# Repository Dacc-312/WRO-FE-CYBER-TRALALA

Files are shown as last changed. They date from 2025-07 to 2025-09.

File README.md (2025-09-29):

Cyber Tralala - WRO Future Engineers 2025
====

We are Cesar Escarrá, Diego Concepción and Christopher Vásquez. We are students from Thomas Jefferson School Of Panama and we are the members of the team Cyber Tralala that competes in the WRO 2025 Future Engineers Category. In this Repository, we share all the information of our project.  

Somos Cesar Escarrá, Diego Concepción y Christopher Vásquez. Somos estudiantes del Thomas Jefferson School y conformamos el equipo Cyber Tralala que participa en la categoria de futuros ingenieros de la WRO. En este repositorio compartimos toda la informacion de nuestro proyecto.  

## Project summary / Resumen del proyecto
  
Tralalerito is our self-driving car built for the WRO 2025 Future Engineers category. Our goal is to design a small, reliable robot that can navigate the Open Course and the Obstacle Course without any human control.  

Tralalerito es nuestro carro autónomo para la categoría Futuros Ingenieros de WRO 2025. Nuestro objetivo es diseñar un robot pequeño y confiable que pueda completar el Desafio Abierto y el Desafio de Obstaculos sin control humano.  

  

The robot uses a mix of simple sensors and a camera to “see” walls and colored signs on the field. It decides which way to turn and how to move using a program we created.  

We focused on making our car robust, simple and easy to maintain so it can handle the challenges during competition.  

El robot usa una combinación de sensores simples y una cámara para “ver” las paredes y las señales de colores en el campo. Con esa información, toma decisiones sobre cómo girar y avanzar usando un programa creado por nosotros.  

Nos enfocamos en que nuestro carro fuera resistente, simple y fácil de mantener para poder afrontar los retos durante la competencia.  

## Table of Content/ Tabla de Contenido 

* `t-photos` contains  photos of the team - Contiene las fotos de nuestro equipo.
* `v-photos` contains photos of the vehicle - Contiene las fotos de nuestro vehículo.
* `video` contains the video.md file with the link to a video where driving demonstration exists - Contiene los archivos con links a videos de youtube con el funcionamiento del robot.
* `schemes` contains one schematic diagrams in form of PNG and Fritzing of the electromechanical components illustrating all the elements (electronic components and motors) used in the vehicle and how they connect to each other - Contiene un diagrama electromecanico en formato PNG y Fritzing ilustrando todos los componentes usados en el vehiculo y sus debidas conexiones.
* `src` contains code of control software for all components which were programmed to participate in the competition - Contiene la programación usada en nuestro vehiculo para participar en la competencia.
* `models` is for the files for models used by 3D printers produce the vehicle elements - Contiene los modelos 3D utilizados para imprimir piezas para nuestro vehiculo.
* `other` is for other files which can be used to understand how to prepare the vehicle for the competition. It includes datasets, hardware specifications, communication protocols descriptions, links for buying, etc - Contiene especificaciones de hardware, protocolos de comunicacion, links de compra y otros.

 ## Team Members / Miembros del Equipo  

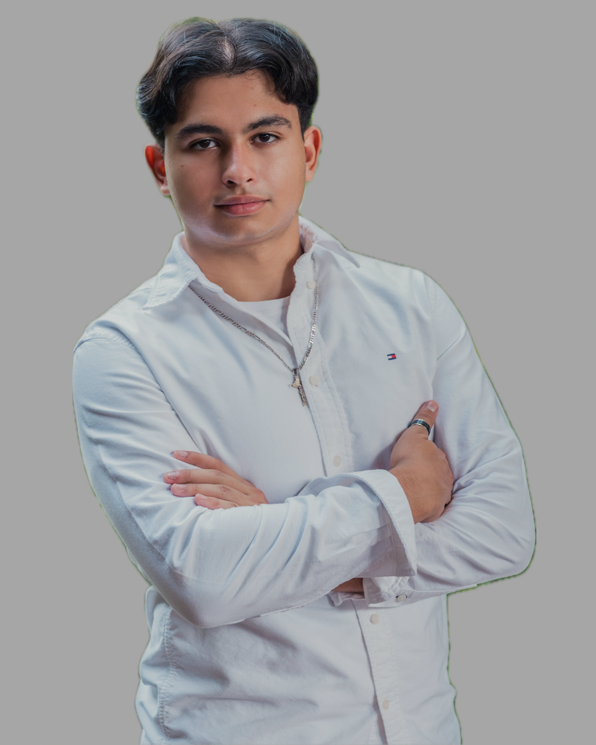
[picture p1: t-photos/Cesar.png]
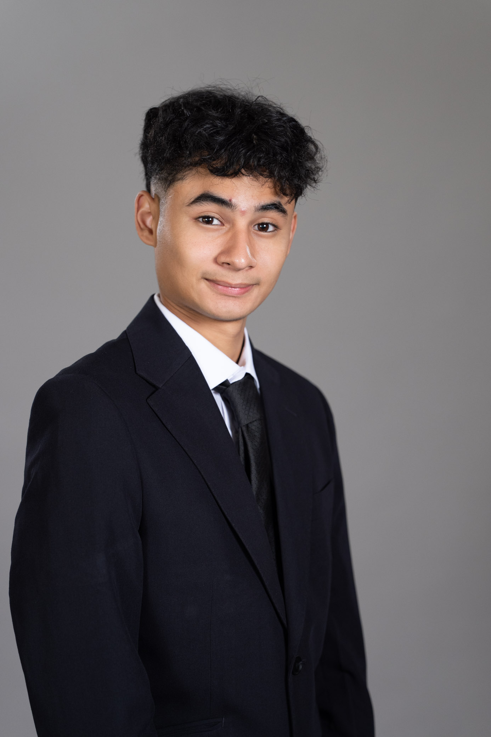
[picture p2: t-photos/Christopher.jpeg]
|  |   |   |
|:---:|:---:|:---:|
| **Diego Concepción**<br>17 years old | **Cesar Escarrá**<br>18 years old | **Christopher Vasquéz**<br>18 years old |

## Robot construction info / Información sobre la construcción y funcionamiento del robot

**Mobility management / Manejo de movilidad**

We decided to use a rear-wheel drive remote control car as the basis for our project. A remote control car provides a fairly resistant chassis in addition to bringing 6v motors for movement and direction, allowing us high speed if necessary. The steering of our car consists of a direct current motor which operates a rack and pinion system to give direction to the front axle.The traction system consist on a simple axle with a gear that is attached to the pinion of the motor. Many cuts were made to the original chassis to be able to remove the original circuits and place our circuits. We also desgined and printed 3D mounts for our sensors and camera. On top of that, we designed and printed a Cybertruck body to give protection to the internal parts and electronics.
  
Decidimos usar como base para proyecto un carro a control remoto de tracción trasera. Un carro a control remoto nos da un chasis resistente, adicional de tener el sistema de tracción y dirección con los motores de 6v necesarios para ello, y nos permite usar el auto a altas velocidades si es necesario. La direccion de nuestro vehículo consiste en un motor de corriente continua que opera un sistema de cremallera y piñon que dan el giro a los ejes delanteros. El sistema de tracción consiste en un eje solido conectado a las 2 ruedas traseras y a un engranaje que recibe el movimiento de el piñon del motor trasero. Le hicimos diversas modificaciones al chasis para poder quitar los controladores y circuitos originales y hacer espacio para colocar los nuestros. Le añadimos soportes impresos en 3D al chasis para poder colocar nuestros sensores y nuestra camara. Adicionalmente, diseñamos e imprimimos en 3D una carroceria de Cybertruck para cubrir y proteger los componentes electronicos y demas componentes internos del vehiculo.

**Power management / Manejo de potencia eléctrica**

For this project we decided to eliminate the car's original power source which was AA batteries and use 2 18650 lithium ion batteries connected in series because they have a much greater discharge capacity than AA batteries, in addition to having more capacity and more voltage (3.7V each one, making a total of 7.4V in series). These batteries are widely used from flashlights to electric vehicles, this way we ensure that it is easy to get chargers and spare parts.

Para este proyecto decidimos eliminar la fuente de poder original del auto que eran 2 baterias AA, y usamos 2 baterias 18650 de iones de litio conectados en serie, porque tiene una capacidad de descarga mucho mayor, aparte de tener una mayor capacidad y un mayor voltaje (3.7V cada una, totalizando 7.4V en serie). Estas baterias son ampliamente usadas, desde en linternas como en vehiculos electricos, así nos aseguramos que podemos conseguir fácilmente cargadores y repuestos.

**Obstacle and sense management / Manejo de visión y obstaculos**

For this project we decided to use hc-sr04 ultrasonic sensors because they are cheap, easy to obtain and have fairly low consumption. We are using two sensors, one on each side, to detect the distance to the walls on the sides so that we can make corner turns and stay without crashing in the open challenge. In the case of the obstacle challenge, the sensors still play a secondary role in helping to turn and prevent the car from crashing into walls.

For obstacle management we decided to use a Huskylens camera. This camera is very intuitive to use and has artificial intelligence which helps with detection, in this case of colors. The camera provides very good integration with the Microbit platform in addition to the ability to program new colors in just seconds.

Para ese proyecto decidimos utilizar sensores ultrasónicos HC-SR04 porque son baratos, fácil de obtener y tienen un consumo muy bajo. Estamos utilizando dos sensores, uno en el lado izquierdo y el otro en el derecho para obtener la distancia hasta las paredes laterales y poder tomar las curvas sin chocar en el desafio abierto. En el caso del desafio de obstaculos, los sensores igual toman un rol secundario en ayudar a girar y prevenir que el vehiculo choque.  

Para detectar los obstaculos, decidimos utilizar una camara Huskylens. Seleccionamos esta camara porque es muy intuitiva y tiene integrada una inteligencia artificial que ayuda con la deteteccion, en este caso de los colores. La camara tiene una muy buena integracion con la prataforma de microbit y tiene la capacidad de aprender colores en segundos.  
  
**Open Challenge Programming / Programación Desafío Abierto**

To program the open circuit, we use simple programming based on the two ultrasonic sensors. First, the ultrasonic variable and the elapsed time in the loop are established to have a constant reading, a conditional is placed to activate the H-bridge so that the rear motor goes forward with a constant speed until the elapsed time is the equivalent to 3 turns, where it stops moving. Now we place a condition, If our sensor detects a distance greater than 1.5 meters to one side, this means that the car must be turned to that side by activating the H-bridge corresponding to that direction of the front motor. Afterwards, if the sensors detect a distance greater than 30 cm on each side (which means that it is in the center) the car will advance straight, otherwise, the car will look for which of the two sides the measurement is less than 30cm to turn in the other direction and rectify.  

Para el circuito sin obstaculos, utilizamos una programacion simple basada en los dos sensores ultrasonicos. Primero, las variables de las distancias y el tiempo transcurrido se establecen en el bucle para tener una medicion constante. Colocamos una condicional para activar el Puente-H para que el motor avance con una velocidad constante hasta que el tiempo transcurrido corresponda al de las 3 vueltas, donde se detiene. Ahora colocamos una condicional, si nuestros sensores miden una distancia mayor a 1.5 metros en un lado, el vehiculo se mueve en esa direccion activando el puente H y por consecuencia el motor para que la direccion gire al lado adecuado. Despues, si los sensores miden una distancia mayor a 30cm en ambos lados (Esto significa que el robot esta en el centro) el carro avanzara recto, sino, el carro va a determinar de que lado la distancia es menor a 30cm para girar en la otra direccion y rectificar.

**Programming challenge obstacles / Programación desafío de obstaculos**

To begin, we first activate the huskylens in I2C protocol to communicate with the microbit and place it in color detection mode. After that, we have a secuence to drive out the parking lot, where it uses the ultrasonic sensors to determine where is the closest wall and then proceeds to go forward and backwards until its completely out of the parking space. In addition, we start with the rear motor at a slightly higher power controlled by pwm to have inertia when starting.

We used 2 loops that run at the same time, one for the steering and one for the movement. In the movement loop, we run a code that simulates a pulse control that gives peaks of power while maintaining a low speed, we did this in order to not get stuck in the case it colides with an obstacle. In the other  loop, we place all the ultrasonic sensor variables and the huskylens sampling,. When it detects “ID1” corresponding to red, it turns to the right until it disappears from the field of view that we established by coordinates, the same with green “ID2” in the other direction. Finally, we put the same ultrasonic distance detection program that we used in the open challenge.

Para comenzar, en el bloque de inicio activamos el protocolo I2C de la huskylens para que se comunique con el microbit y se programe en modo de detección de color. Despues, tenemos la secuencia para salir del estacionamiento, donde utiliza los sensores ultrasonicas para determinar cual es la pared mas cercana y poder proceder a avanzar y retroceder hasta salir del estacionamiento. Adicionalmente, colocamos el motor trasero a una potencia mayor para tener mas inercia al iniciar.  

Usamos 2 bucles que se ejecutan simultaneamente, uno para la direccion y una para el movimiento. En el bucle del movimiento, ejecutamos un codigo que simula pulsos para tener picos de potencia mientras mantenemos una velocidad baja, asi podemos desatascarnos en caso de colisionar con un obstaculo o una pared. En el otro bucle, colocamos las variables de las distancias medidas por los sensores y el muestreo de la Huskylens, y colocamos las condicionales para la detección de colores de la Huskylens. Cuando la Camara detecta el ID1 correspondiente al color rojo, el vehiculo dobla hacia la derecha hasta que desaparece el ID de el campo de vision que establecemos con coordenadas, lo mismo pasa con el verde o ID2 en la otra direccion. Finalmente, despues de las condicionales de los obstaculos utilizamos el mismo codigo que en el desafio abierto.

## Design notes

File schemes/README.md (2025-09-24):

Electromechanical diagram/ Diagrama electromecanico
====

This directory contains the schematic diagram in form of .PNG and .FZZ (Fritzing) of the electromechanical components illustrating all the elements (electronic components and motors) used in the vehicle and how they connect to each other.  

  Este directorio contiene el diagrama en formato .PNG y .FZZ (Fritzing) de los componentes electromecanicos del vehiculo ilustrando todos sus elementos (motores y componentes electricos) y sus debidas conexiones.  

  Cyber Tralala-Wiring Diagram-Diagrama de cableado

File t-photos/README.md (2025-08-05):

Team's photos/Fotos del equipo
====

Here you can see the photos of the team members.   
  
En este directorio contiene las fotos de los miembros de nuestro equipo.  

All the team/Equipo Completo
====  
   
Team Photo-Foto Equipo 1 (1)

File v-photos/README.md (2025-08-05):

Vehicle's photos/Fotos del vehiculo
====

This directory contains photos of the vehicle (from every side, from top and bottom).  
  
Este directorio contiene las fotos del vehiculo (de cada lado, incluyendo por arriba y por abajo).

Top View-Vista Superior (1)
Right View-Vista Derecha (1)
Left View-Vista Izquierda (1)
Front View-Vista Frontal (1)
Bottom View-Vista Inferior (1)
Back View-Vista Trasera (1)
Back View-Vista Trasera (1)
Front with Case-Vista Frontal con carroceria (1)
Back with Case-Vista Trasera con carroceria (1)

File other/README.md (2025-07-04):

Technical Specifications/Especificaciones tecnicas
====  

Controller: Microbit V2  
Specifications:

64 MHz ARM Cortex-M4 processor  
512KB Flash Memory  
RAM 128KB  
5x5 Red LED Matrix  
2 programmable buttons + a touch logo  
MEMS microphone and LED power indicator  
Integrated temperature and light sensors, plus accelerometer, compass and speaker  
2.4 GHz radio to communicate micro:bits  
Bluetooth BLE 5.0  
25-pin comb connector to add more sensors  
4 dedicated GPIO pins for PWM, I2C, SPI, and external power  
Three digital/analog inputs/outputs accessible via alligator cables  
Two 3V/GND power rings  
Dedicated I2C port for peripherals  
MicroUSB connector (5V)  
JST-PH connector compatible with LiPo batteries (3V)  
Power/reset button with status LED  
Maximum available current of 200 mA for peripherals  
Programmable with C++, MakeCode, Python and Scratch.  
Dimensions: 50mm-45mm-7mm  
  
Power Distributor: Microbit Expansion Board  
Specifications:  
  
20 3PIN ports (GND, VCC and Signal)  
1 I2C port  
5 Vdc (x USB) / 7 to 9 Vdc (x 2.1 mm jack)  
Voltage output to sensor: 3.3 / 5 Vdc  
Dimensions: 55mm-65mm-10mm  
  
Motor Driver: L298N  
Specifications:  
  
Chip: L298N  
Channels: 2 (supports 2 DC motors or 1 PAP motor)  
Logic voltage: 5V  
Power voltage (V motor): 5V - 35V DC  
Current consumption (logical): 0 to 36mA  
Current capacity: 2A (peaks up to 3A)  
Maximum power: 25W  
Dimensions: 43mm-43mm-27mm  
  
Size of our car  
  
Length: 24.5cm  
Width: 11cm  
Height: 13.5cm  
Scale: 1/14  
Max speed: 20Km/h  
Operating voltage: 7.4v  
Battery model: 18650 x2  
  
Ultrasonic Sensor HC-SR04  
  
Specifications  
Operating Voltage: 5V   
Quiescent current: <2mA  
Working current: 15mA  
Measuring range: 2cm to 450cm  
Accuracy: +- 3mm  
Opening angle: 15°  
Ultrasound frequency: 40KHz  
Minimum TRIG trigger pulse duration (TTL level): 10 μS  
Output ECO pulse duration (TTL level): 100-25000 μS  
Dimensions: 45mm-20mm-15mm  
Note: Minimum waiting time between one measurement and the start of another 20ms (50ms recommended)  
  
Camera that we use to sort the obstacles: HuskyLens  
Specifications  
  
Processor: Kendryte K210  
Image Sensor: SEN0305 HuskyLens: OV2640 (2.0Megapixel Camera)  
Supply voltage: 3.3~5.0V  
Current consumption (TYP): 320mA@3.3V, 230mA@5.0V (face recognition mode; 80% backlight brightness; fill light off)  
Connection interface: UART; I2C  
Display: 2.0-inch IPS screen resolution 320*240  
Built-in algorithms: face recognition, object tracking, object recognition, line tracking, color recognition, label recognition  
Dimensions: 52mm-44.5mm  
  
Note: The camera is connected by the I2C communication protocol. Its connection is specified in the diagrams section.

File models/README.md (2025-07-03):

3D Designs and Models/Diseños y Modelos 3D
====  

This directory contains the STL files of the 3D Models and Designs (A case for the camera and a mount for the ultrasonic sensors) that we printed and used in our vehicle.  
  
Este directorio contiene los archivos STL de los modelos 3D (Un Soporte para los sensores ultrasonicos y un protector para la camara) que utilizamos para imprimir y montar en nuestro vehiculo.

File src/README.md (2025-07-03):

Control software/Programacion
====

This directory contains code in Python and images of the blocks for control software which is used by the vehicle to participate in the competition and which was developed by the participants.  
  
Este directorio contiene la programacion en Python y en bloques que desarollamos para ser utilizada en nuestro vehiculo para la competicion.

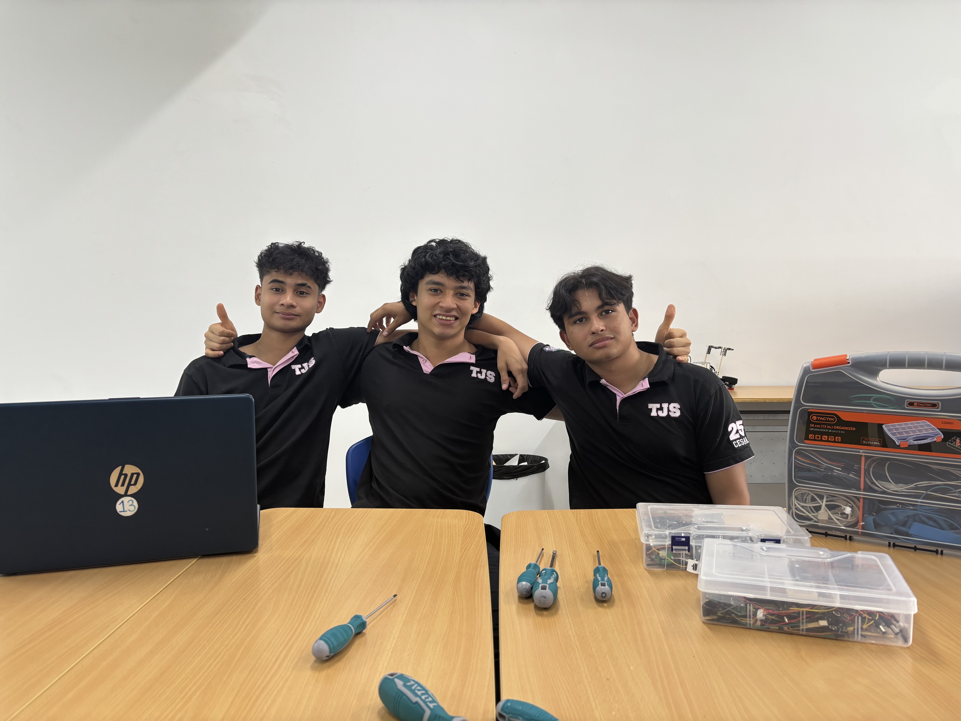
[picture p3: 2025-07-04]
t-photos/Team Photo-Foto Equipo 1.jpeg

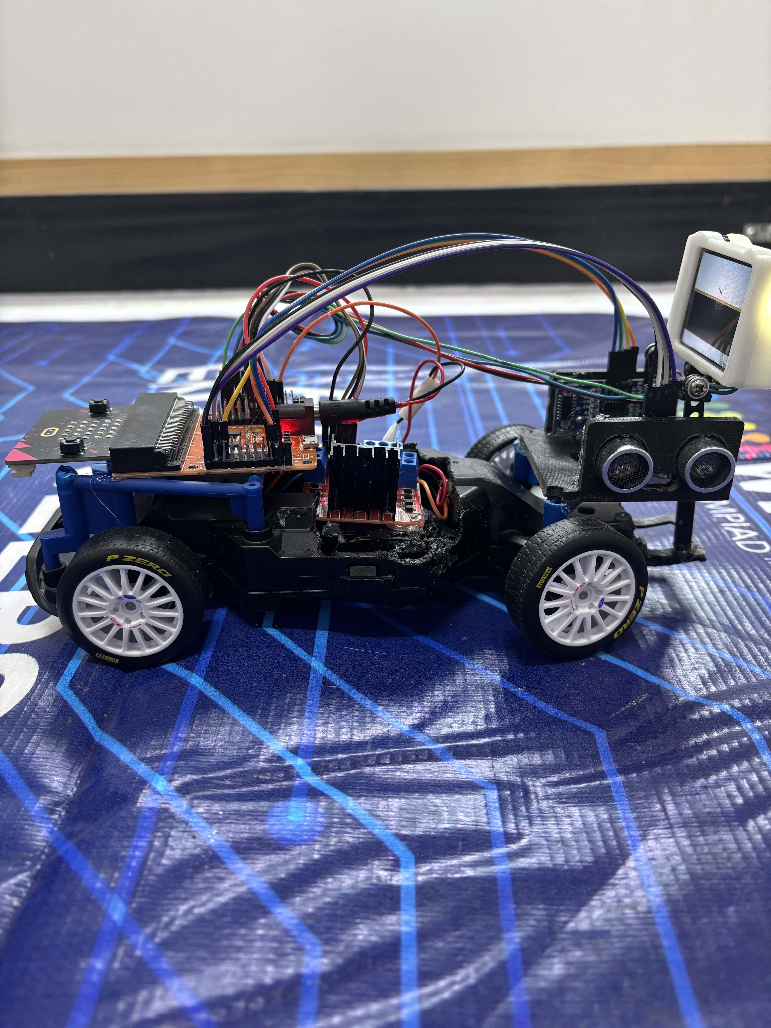
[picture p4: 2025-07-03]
v-photos/Right View-Vista Derecha.jpeg

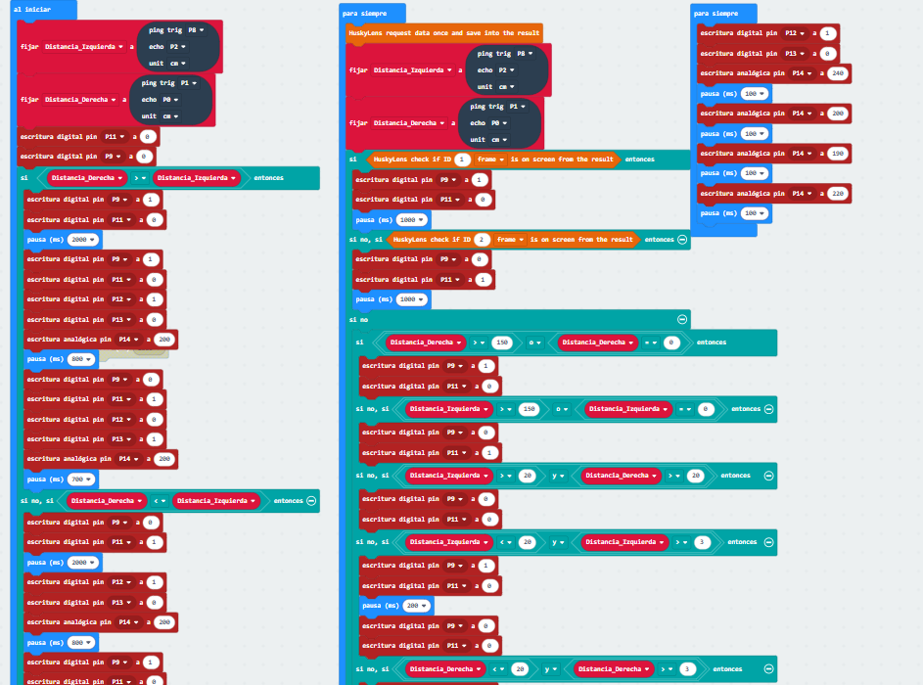
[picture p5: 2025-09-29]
src/Obstacle round blocks 1.png

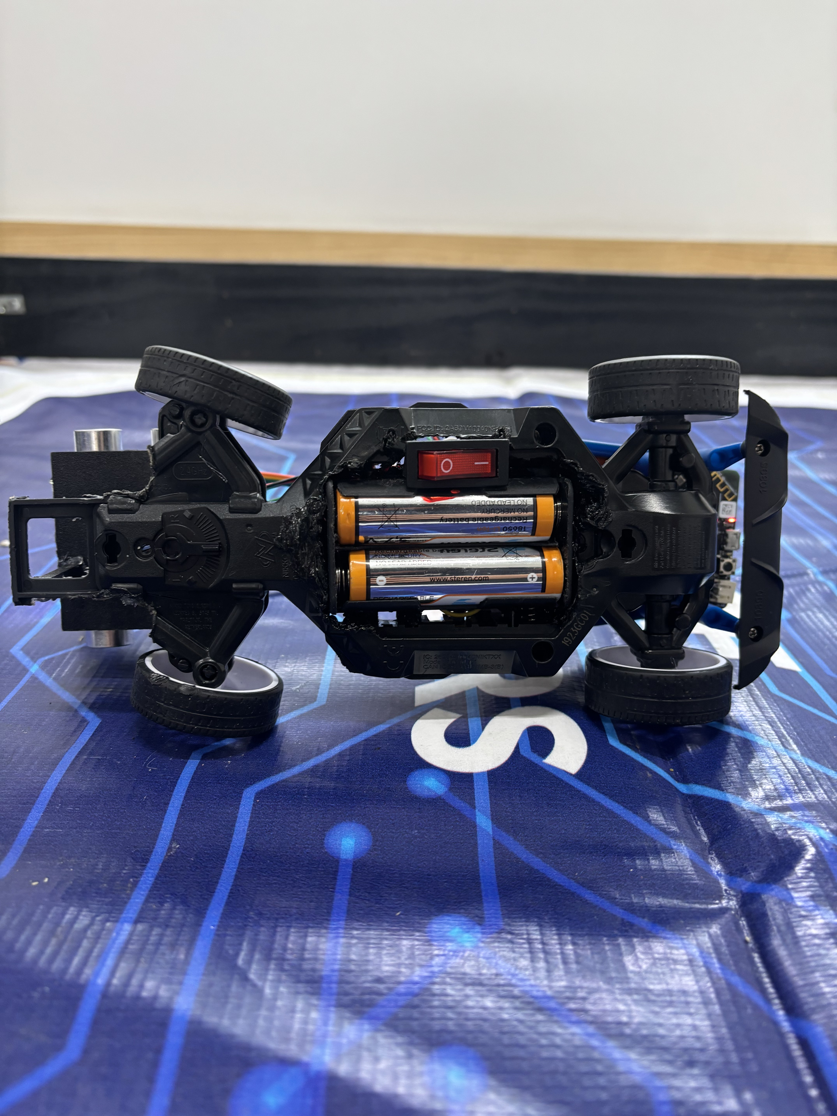
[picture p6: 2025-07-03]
v-photos/Bottom View-Vista Inferior.jpeg

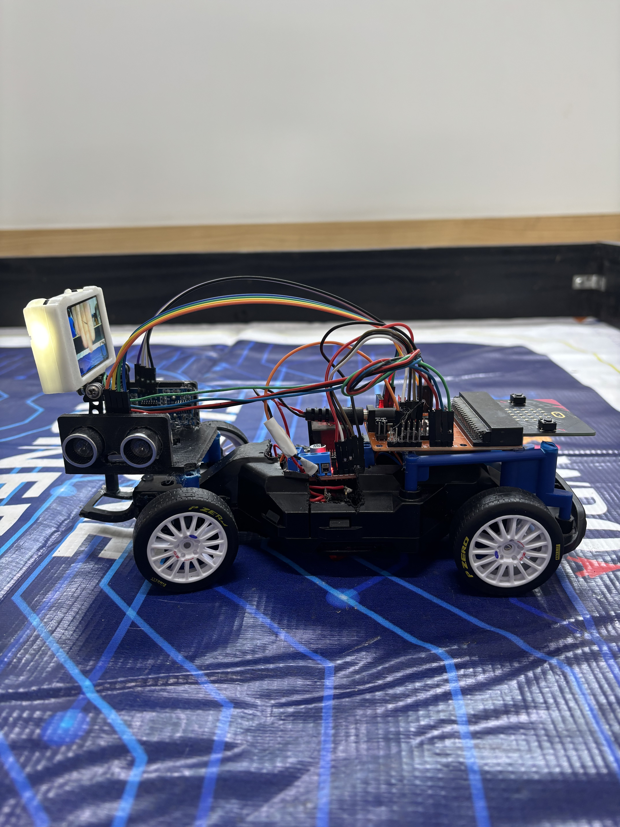
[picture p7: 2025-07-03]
v-photos/Left View-Vista Izquierda.jpeg

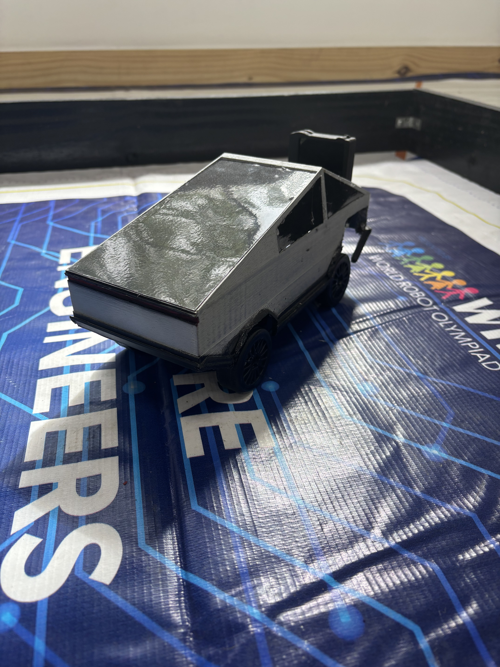
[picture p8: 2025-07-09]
v-photos/Back with Case-Vista Trasera con carroceria.jpeg

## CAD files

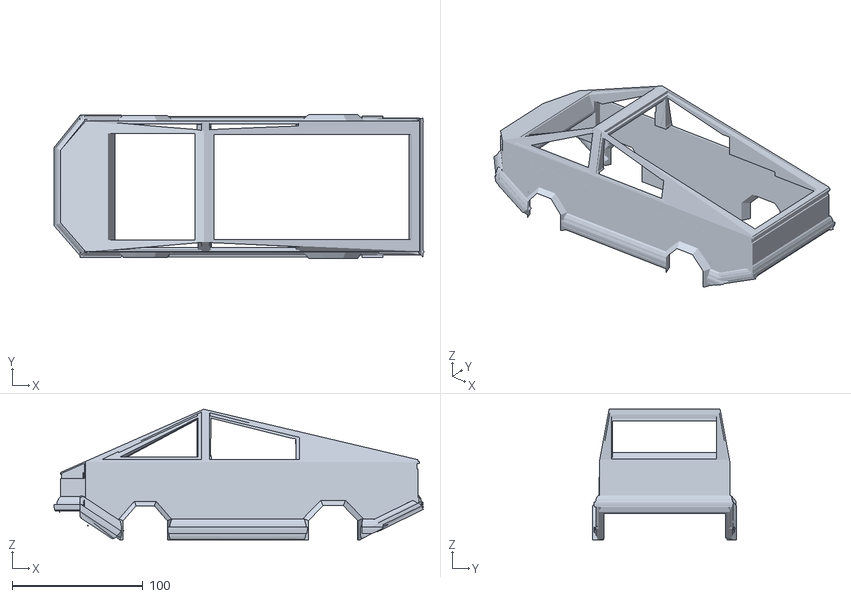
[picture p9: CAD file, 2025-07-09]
models/Cybertruck-Cyber Tralala.stl
283.4 x 110.1 x 100.0

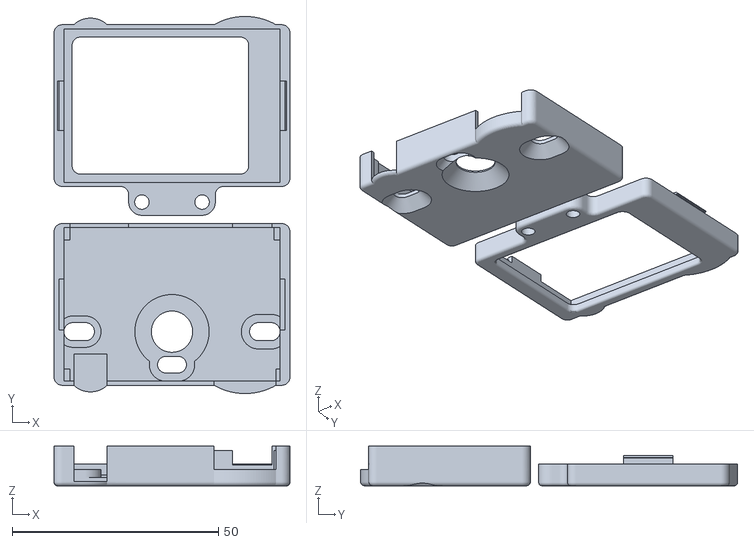
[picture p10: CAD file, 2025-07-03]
models/Huskylens (Camera) Case-Cyber Tralala.stl
57.2 x 91.4 x 9.60

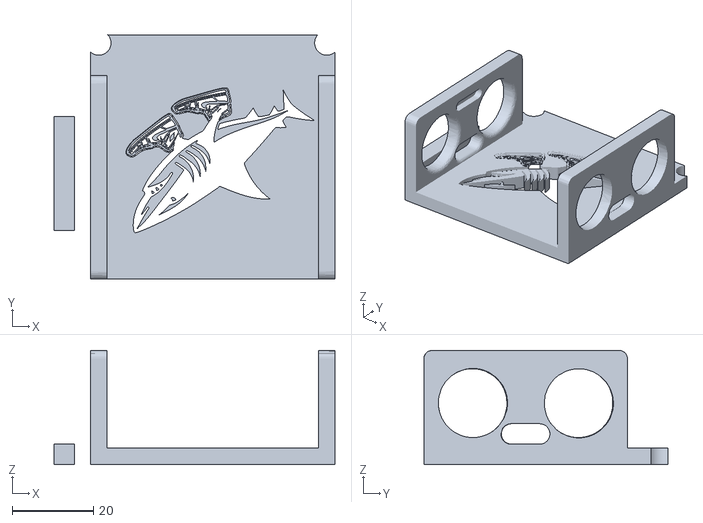
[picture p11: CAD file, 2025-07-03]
models/Sensor Mount-Soporte Sensores-Cyber tralala.stl
69.0 x 60.0 x 28.0

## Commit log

2025-07-03 Create Expansion Board-Tarjeta de expansion Link
2025-07-03 Create HC-SR04 Sensor Link
2025-07-03 Create L298N Motor Driver-Controlador Link
2025-07-03 Rename Expansion Board-Tarjeta de expansion Link to Expansion Board-Placa de expansion Link
2025-07-03 Create Huskylens Camera Link
2025-07-03 Rename IMG_8089.jpeg to Top view‑Vista superior.jpeg
2025-07-03 Create Open Run Code‑Codigo desafio abierto
2025-07-03 Create Obstacle Round Code‑Codigo Ronda Obstaculos
2025-07-03 Rename Obstacle Round Blocks 2‑ Bloques ronda obstaculos2.png to Obstacle Round Blocks 2‑ Bloques ronda obstaculos 2.png
2025-07-03 Create How to Connect L298N Driver-Como conectar modulo L298N
2025-09-29 Update Obstacle Round Code‑Codigo Ronda Obstaculos
2025-09-30 Update Open Run Code‑Codigo desafio abierto
